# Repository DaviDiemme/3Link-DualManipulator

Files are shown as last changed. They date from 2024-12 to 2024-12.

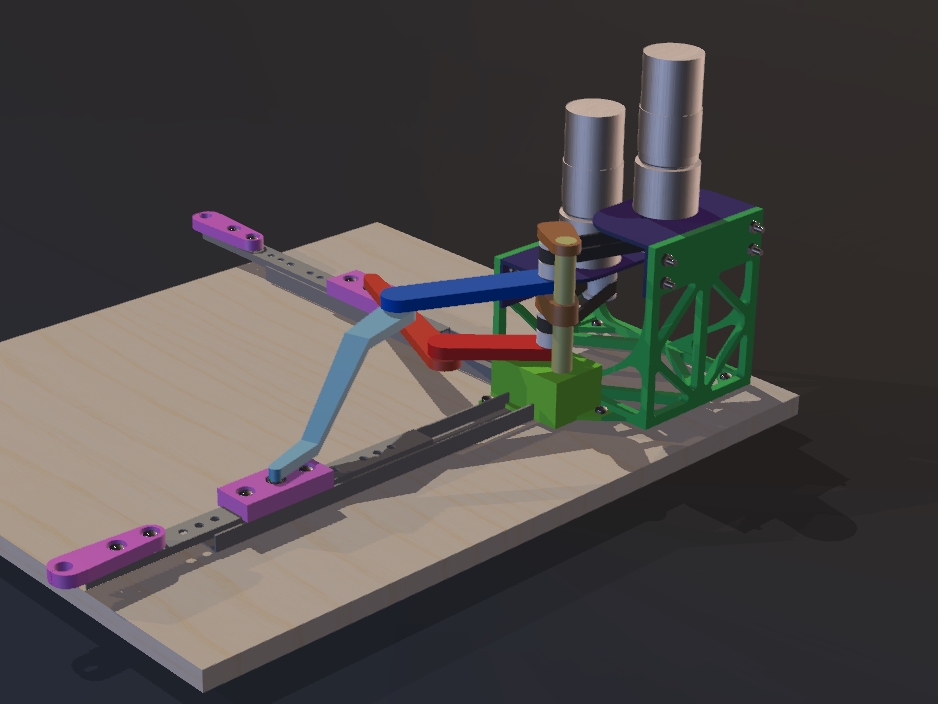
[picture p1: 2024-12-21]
images/robot render1 8.jpg

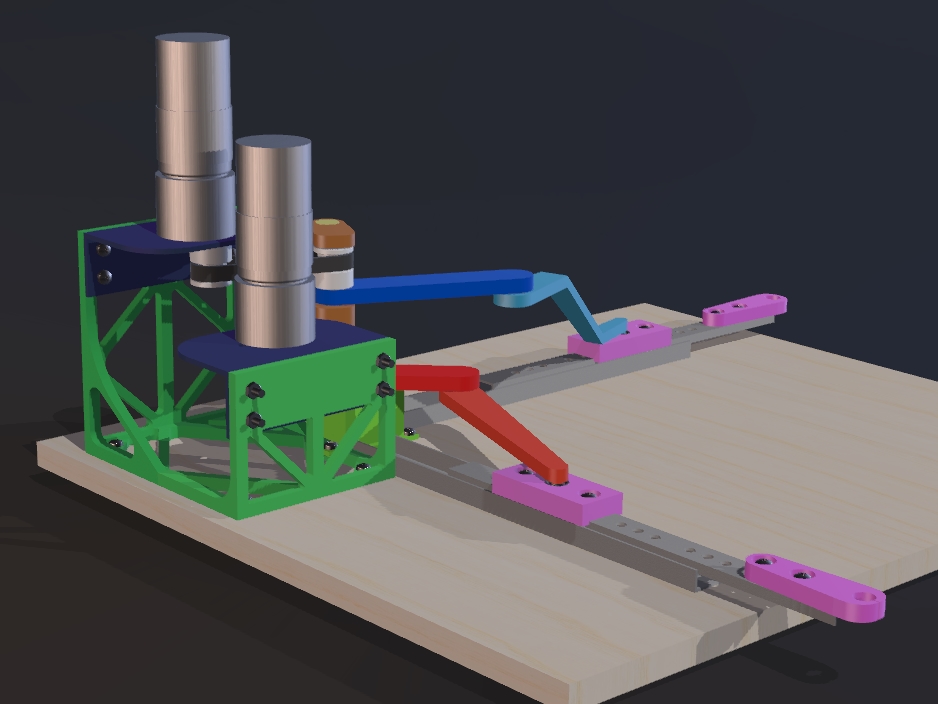
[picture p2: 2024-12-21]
images/robot render1 5.jpg

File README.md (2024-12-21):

robot render1 7

The device consists of a dual three-link manipulator with 2 actuators and 2 end-effectors on 
perpendicular axes.
The design process starts with the study of the 2D model of the robot and the evaluation of 
its kinematics. The workspace of the robot is then explored and, after considering several 
concepts, the most suitable design is assessed and explained.

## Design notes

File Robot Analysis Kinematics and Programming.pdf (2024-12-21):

Davide De Marco – DaviDiemme - GitHub - 122024

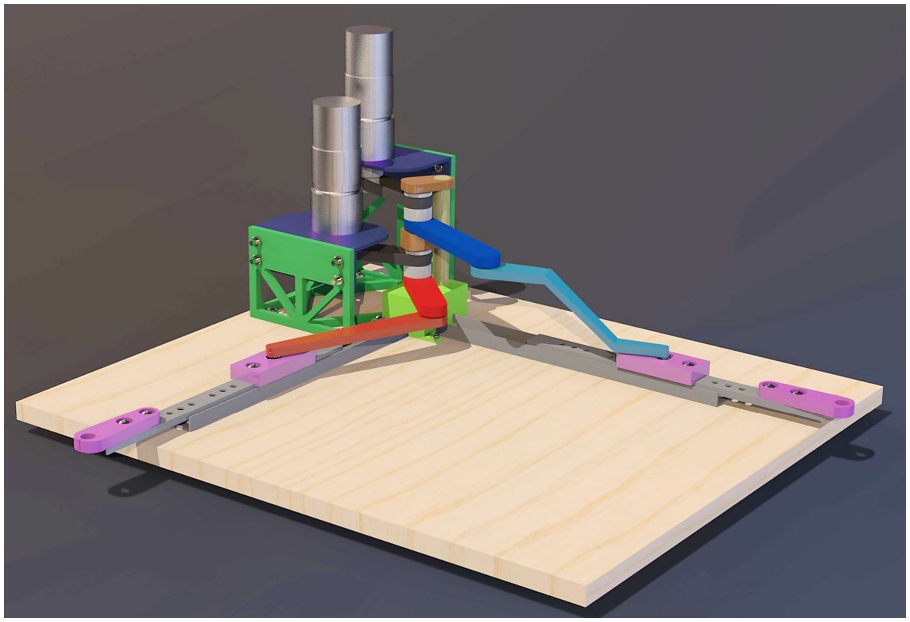
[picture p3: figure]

0

Introduction

The device consists of a dual three-link manipulator with 2 actuators and 2 end-effectors on perpendicular axes.

The design process starts with the study of the 2D model of the robot and the evaluation of its kinematics. The workspace of the robot is then explored and, after considering several concepts, the most suitable design is assessed and explained.

The programming is executed using MATLAB Simulink, also for the construction of the kinematics block diagrams.

First a closed-loop system is run to test the application of PID controller for running the DC motor, then the robot kinematics functions are built and implemented in the control system.

Tools and Components

The motors used are 2 simple EMG30 12 volts brushed motors, equipped with encoders and a gearbox reduction of 30:1, the encoders are used for the feedback signal in the control system.

The motors are driven by a RKL298 PCB, it can power up to two motors with the use of an external DC power supply and consists of an H-bridge drive chip that adjusts the rotation of each motor by controlling the polarity of the voltage applied to it, the sense of rotation depends on the combination of two inputs pins that come from the microcontroller. The speed of the motor is also regulated by the microcontroller sending Pulse Width Modulation -PWM- pulses to the motor driver.

1

The microcontroller stated is the Launchpad F28069M board by Texas Instruments interfaced with MATLAB, the code is generated by Code Composer Studio on the basis of a block diagram model built on Simulink.

Robot Kinematics
Due to the structure of the robot, the kinematics of the two manipulators is the same but on different axis and angles. Note that the shape of the robot leads to establish some limits to the movement of the actuators.
Each manipulator consists of 3 links and 3 joints, the first joint is attached to the actuator on the base, while the last one is fixed on a linear slider. The third link with the end-effector move along a defined axis and therefore the rotational movement of the actuator is converted into linear displacement. The two manipulators have a similar shape but with links of different lengths, that affect their workspace and movement.
Set 1)

The first manipulator lies on the horizontal axis.
The actuator is placed
on the base, and it is
considered as the origin
of the x-axis on which
the end-effector moves.

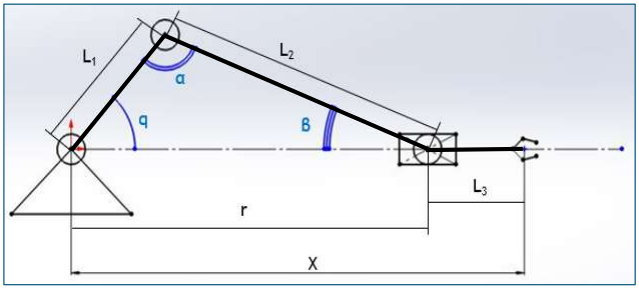
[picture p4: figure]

Forward Kinematics
Forward kinematics consists in the derivation of the total displacement X for any given angle of q. The lengths of the links are predefined while the angles change, of which only one is known.
The total displacement X is considered as the sum of L3 and the hypotenuse r of the triangle.

### 1. X = r + L

Two sides and one angle of the triangle are known; hence the third side r can be found using a few trigonometric functions:
From sine rule:
2.
=

=

To find r, angle α is needed, and it is derived from the subtraction of the triangle’s angles to the total of 180°.
First, angle β is calculated from sine

### 3. sin β =

and

Schematics for kinematics of first manipulator

2

### 4. β = sin(

sinq)

Now the third angle is derived

### 5. α = 180 − q − β

And r can be calculated as

### 6.1. r =

or 6.2. r =

Thus, the resultant displacement is equation 1. with the r found in either 6.1 or 6.2. Inverse Kinematics
Inverse kinematics is the derivation of the angle of the actuator q needed to achieve a desired displacement in X.
As for forward kinematics, the total displacement X is the sum of L3 and r, so for the solution of q, r is derived from X

### 7. r = X − L

Cosine rule can be applied to the triangle as in equation 8.

### 8. L

= r
+ L
| − 2rL cos q

From this equation, the angle q can be simply derived:

### 9. cosq =

and

### 10. q = cos(

)

For inverse kinematics, when coming to the resolution of the final angle, always the smallest value is taken, e.g. if cos¹
2

= 60° or 300° only 60 is considered. The angle of the first actuator is limited from 0 to 90°.

3

Set 2)

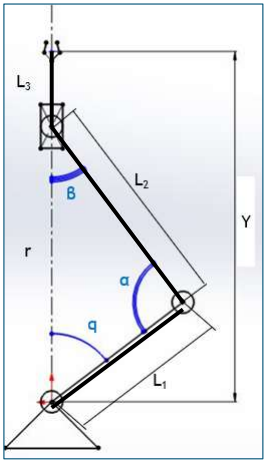
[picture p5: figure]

The second manipulator lies on the vertical axis. The actuator is placed on the base, aligned with the one of set 1, and it is considered as the origin of the y-axis on which the end-effector moves.
Forward Kinematics
Forward kinematics is the computation of the total displacement Y for a given angle q.
The total displacement Y is defined as

### 11. Y = r + L

Equations from 2 to 6 apply in the same way, but with the respective lengths and angle q, and the resulting r is used in equation 11.
Inverse Kinematics
Inverse kinematics is the derivation of the angle of the actuator q needed to achieve the desired vertical displacement in Y.

### 12. r = Y − L

Equations 8 to 10 are used in the same way, but with the respective lengths applied, and the resulting angle is always the smallest between y-axis and the first link L1.
Note that the value of second actuator is considered as negative and is limited from 0 to 60°. Workspace Analysis
The workspace derived from the robot kinematics is quite simple: the two end-effectors move along two perpendicular axes x and y. The robot moves on a 2D plane and has a total of 2 degrees of freedom.
Since, for building reason, limits are set to the actuators’ angle, the workspace only depends on the lengths of the links.
The workspace on the 2 axes goes from the minimum extension of

### 13. X = L

− L

+ L for q = 90°

### 14. Y =

L2 sinα
sinq + L for q = 60°

To the maximum of

### 15. L + L + L for q = q = 0°

For the prototype design the following lengths are used, in millimetres (mm):
SET | LINK 1 | LINK 2 | LINK 3
1 | 50 | 100 | 135
2 | 75 | 100 | 105

Schematics for kinematics of second manipulator

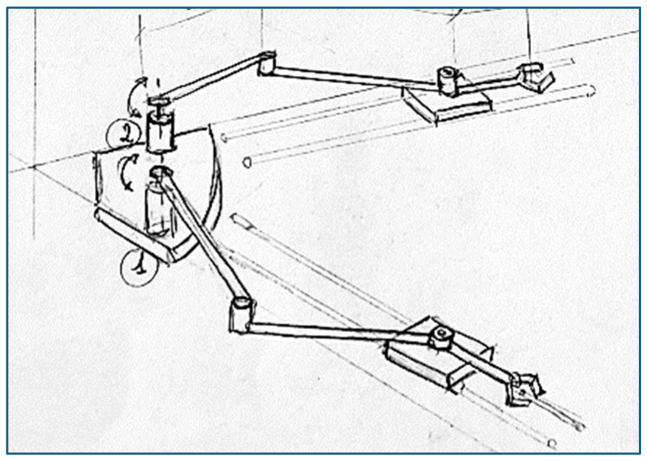
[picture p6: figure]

4

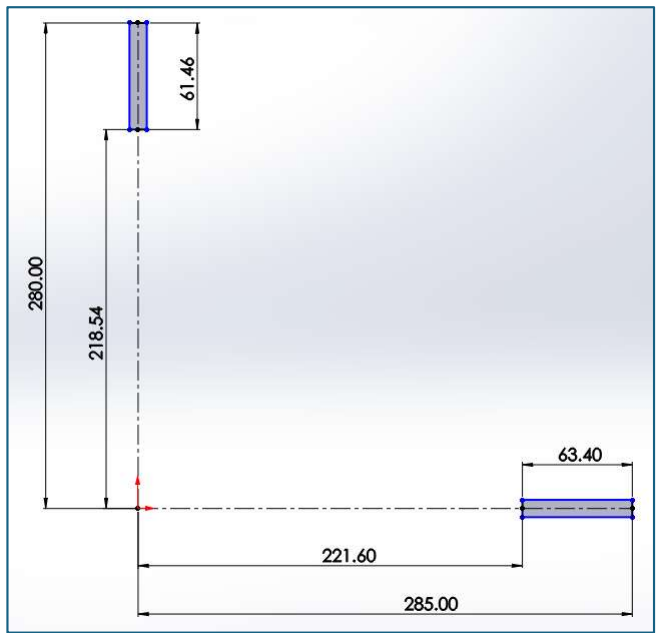
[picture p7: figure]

The workspace measured seems small and very limited, for the two manipulators it appears to be just above 60 mm.
This happens due to the concept and the application of the robot, the actuators cannot rotate fully otherwise there would be conflicts between the different parts that would interfere with each other, preventing the free movement of the manipulators.

General Design and Concept
The robot lies on a 2D plane and has 2 degrees of freedom which correspond to the linear movement of the end-effectors on the two axes of the plane. The first joints of the two manipulators are those connected to the actuators, they are placed on the base, and they are aligned to the same vertical z-axis, going out of the workspace plane.
The end joints and the two end-effectors are fixed on
linear slides; hence the third link is made up of a
carriage, the slide and the end effector. The rotational
movement of the joints is allowed by the use of small ball bearings.
For each actuator, the transmission of angular motion can be ensured by either different gear systems or with pulleys and belt between the motor and the first joint. For the purpose of this robot, the belt and pulley system is chosen as easy to make and accurate. Small and precise gear systems are difficult to print unless a high precision printer is used. Therefore, the two motors can be positioned away from the base but at a defined height that ensures the correct coupling of the belt on the pulleys.
For this concept, the two motors are fixed on the respective mounting brackets that are installed on vertical supports that holds the motors in position, at the correct height, and upside-down.

Workspace drawing with measures

Robot general concept sketch

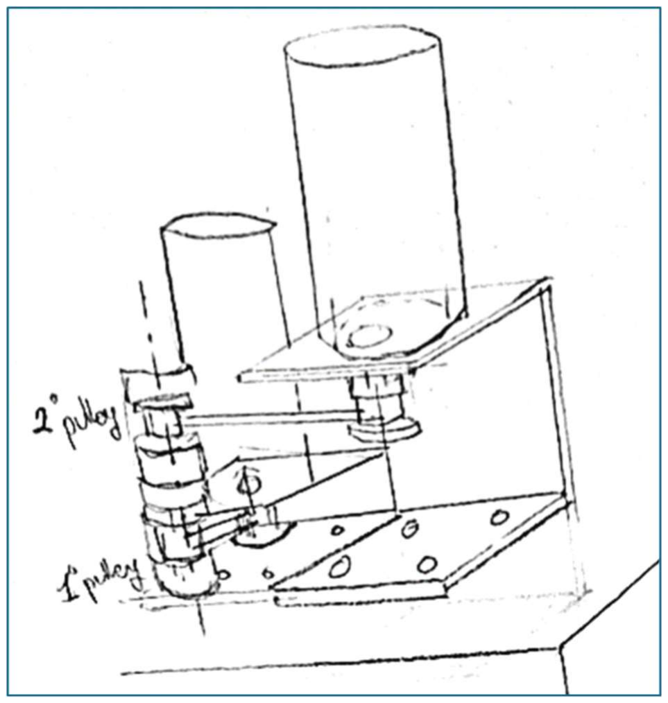
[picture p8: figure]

5

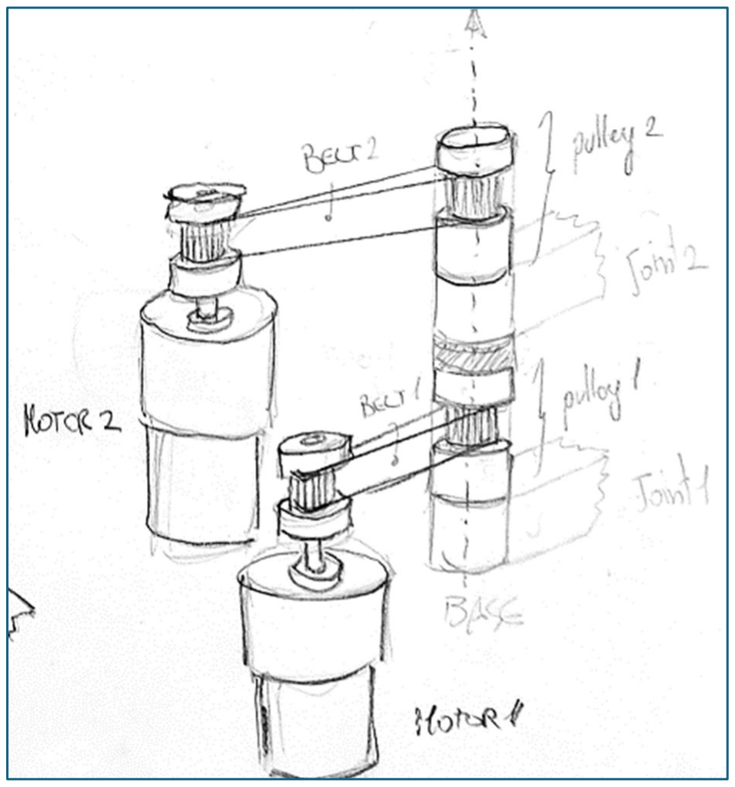
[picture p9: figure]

MATLAB Control Simulation
The program consists of a Simulink model which includes a closed-loop system with PID controller. The controller that takes the angular position of the motor from the encoders, compares it with a given input value and finally delivers a suitable voltage to achieve the exact position. The values of both the reference and the angular position are read in degrees, while the output signal from PID controller is in volts.
The control system design starts with the control test of one DC motor driven by a PID controller implemented within the program. The robot kinematics is then introduced, the respective block diagrams are assembled on Simulink, and subsequently implemented within the motor control diagram.

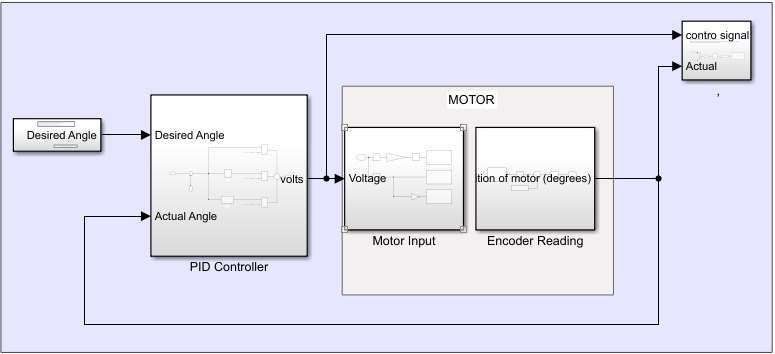
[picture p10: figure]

Control Diagram for one DC motor with PID controller
The PID - Proportional Integral Derivative - control consists in the regulation of a system’s behaviour based on the difference - error - between input signal and the real output signal achieved by the system. The controller is made up of three terms: the error, taken as function of time e(t), its integral and its derivative forms. The three components are first adjusted by some gain values, respectively Kp, Ki and Kd, and then added together to produce the appropriate control signal.

sketch of the pulley and belt system for motion transmission

sketch of the supports for the motors

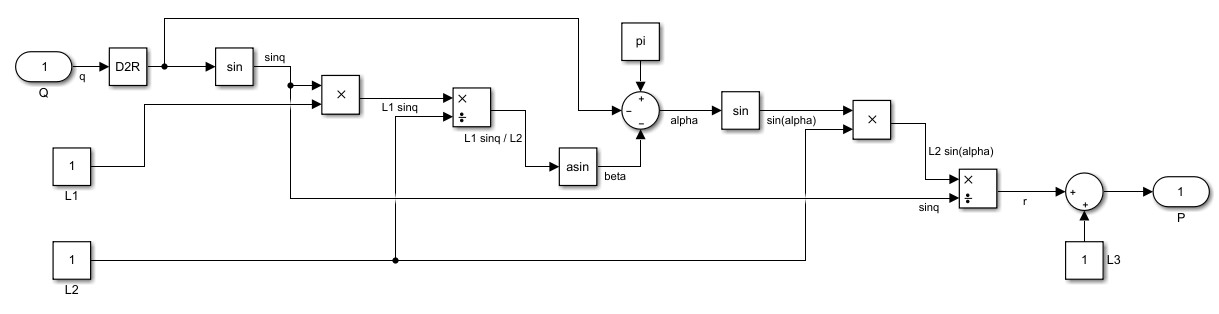
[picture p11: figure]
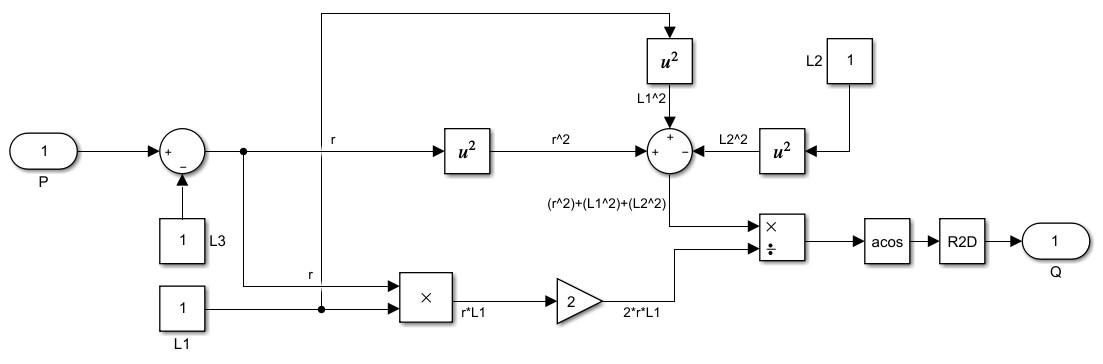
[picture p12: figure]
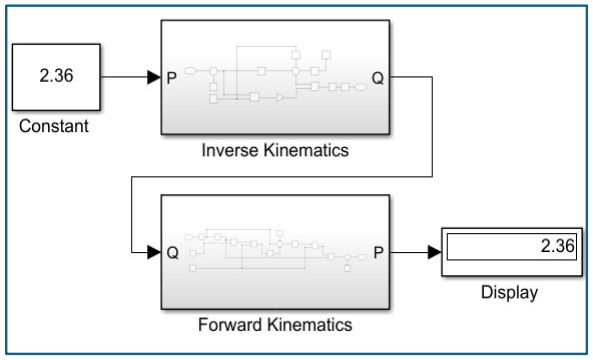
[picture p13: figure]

6

Once the program is uploaded on the board, the ‘desired angle’ and ‘actual angle’ signals are data exchanged between the microcontroller and the software through a serial communication port. By studying this system, the PID controller is tuned, and the gain values are set as the most suitable for the majority of motor angles and applications.
Robot kinematics is built and tested on Simulink. The block diagrams represent the mathematical equations for the forward and inverse kinematics.

Simulink block diagram for forward kinematics

Simulink block diagram for inverse kinematics
It is important to consider that for the kinematics calculations on Simulink input angles must be converted from degree to radians, vice versa for output angles. P stays for position of end-effector while Q is the angular displacement of the actuator.
The two block diagrams are referred to as subsystems, and they are inserted in the same Simulink model and connected together to verify that the outcome of the calculations is always correct for both subsystems.

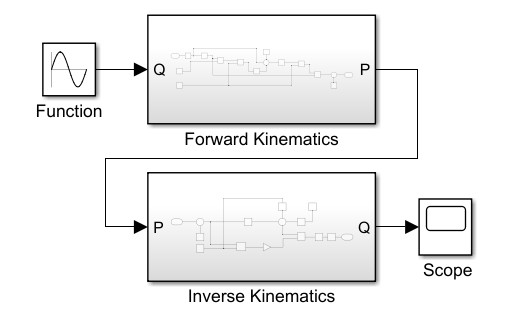
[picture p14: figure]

kinematics results check 1 | kinematics results check 2

7

Once the kinematic blocks have proven to work correctly, the algorithms are implemented in the Simulink control diagram with the PID controller for the DC motor.

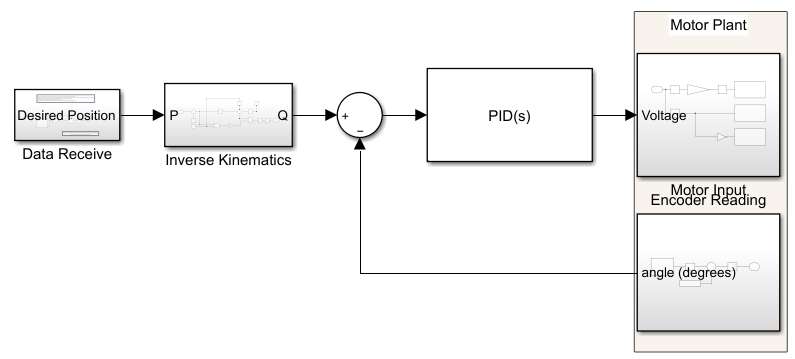
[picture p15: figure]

Simulink block diagram of kinematics PID controller for the robot
The two kinematics blocks can be interchanged according to the application of the device, or they can be used together, changing the type of error signal:

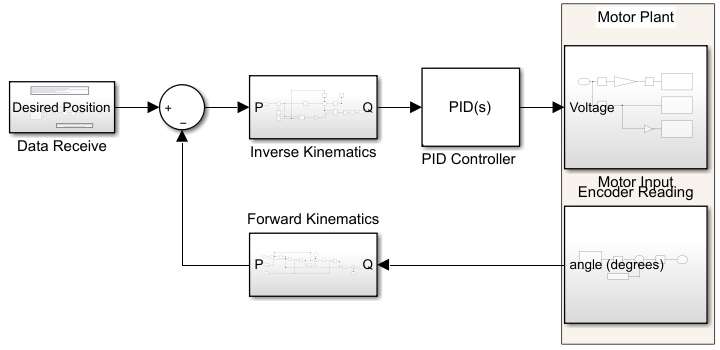
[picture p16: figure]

Simulink block diagram of kinematics PID controller for the robot 2

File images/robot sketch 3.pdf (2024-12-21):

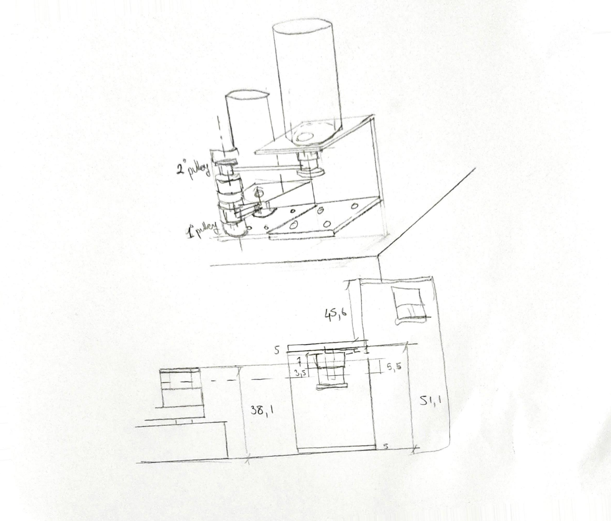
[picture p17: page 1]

6 | o

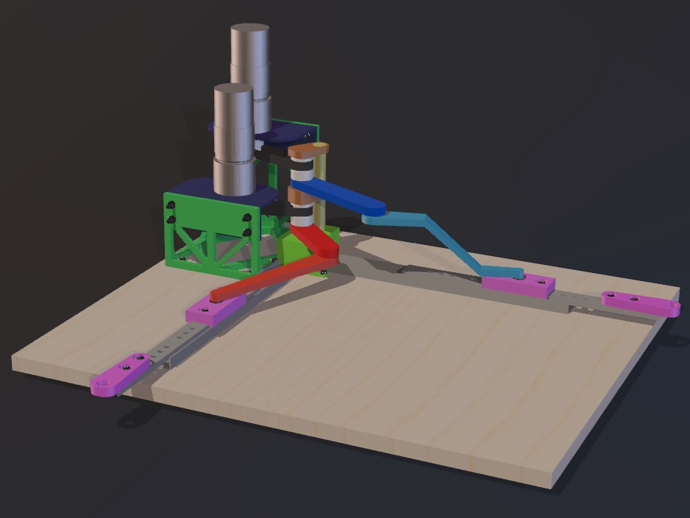
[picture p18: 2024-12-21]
images/robot render1 7.jpg

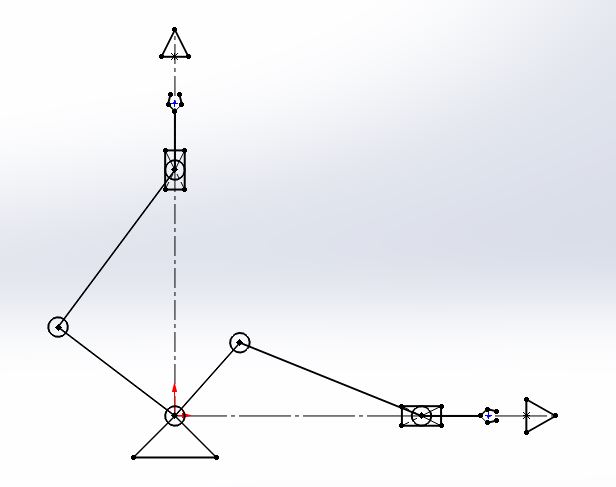
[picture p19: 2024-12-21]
images/2D first sketch.JPG

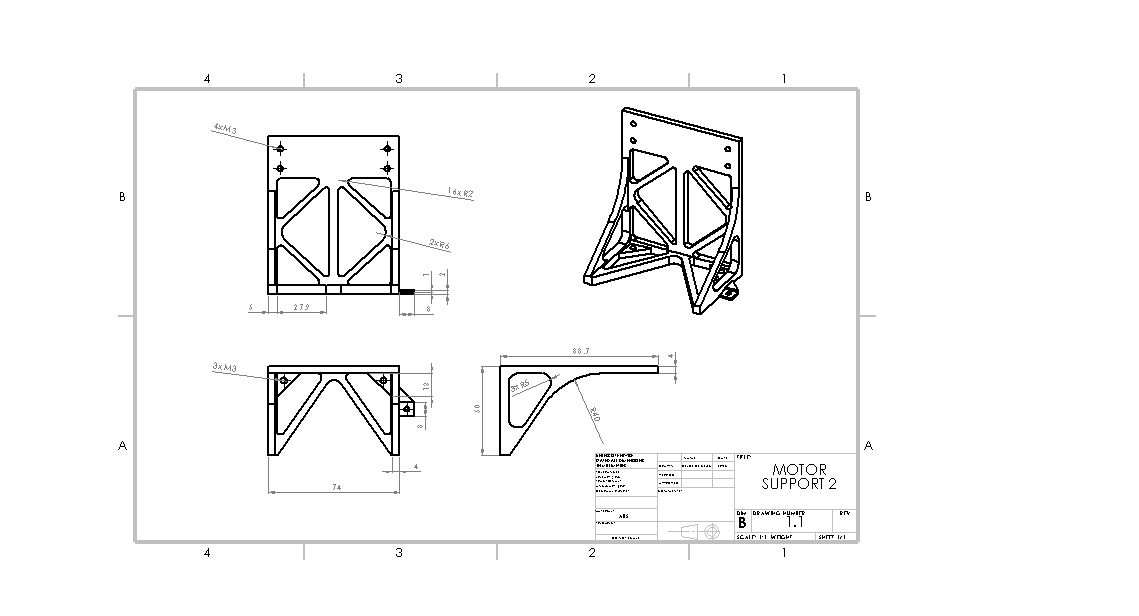
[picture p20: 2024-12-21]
technical drawings/base motor2 drawing.JPG

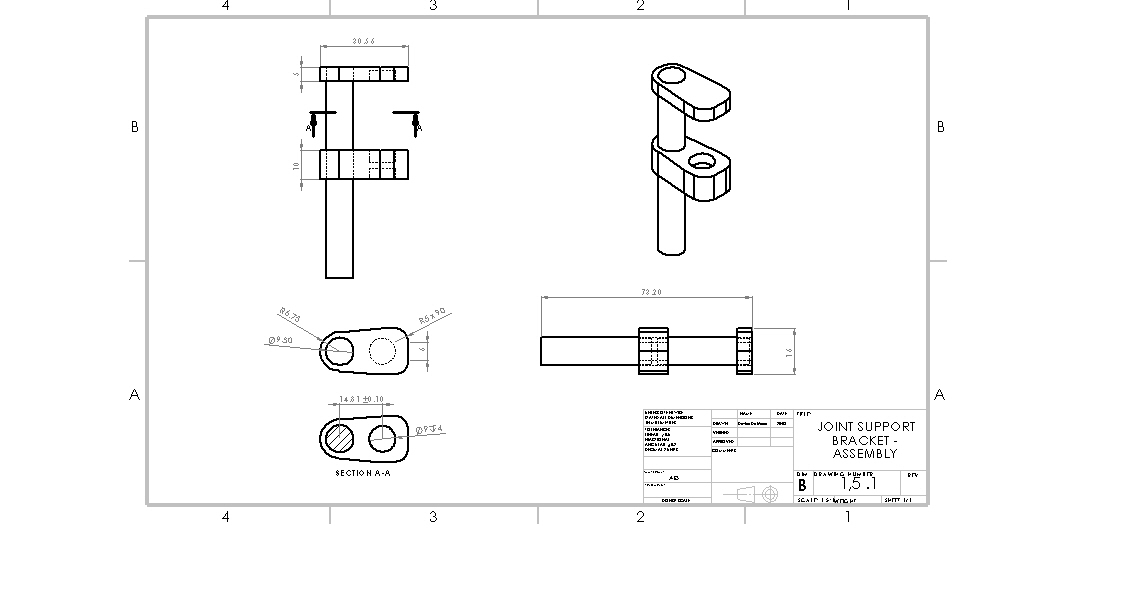
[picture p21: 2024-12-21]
technical drawings/joint support bracket drawing.JPG

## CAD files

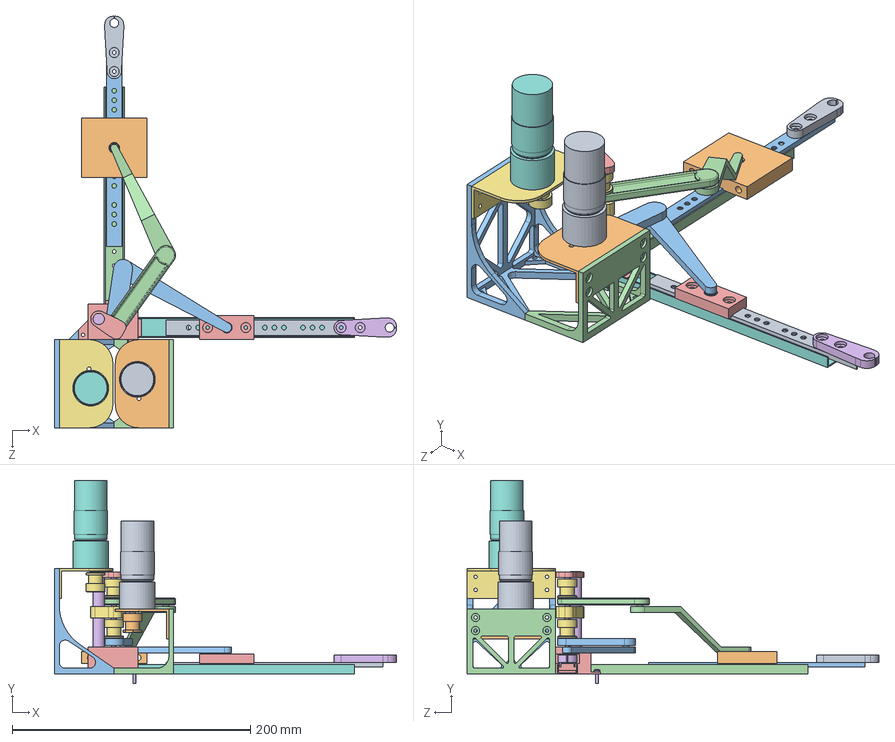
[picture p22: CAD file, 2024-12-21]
SolidWorks parts/Assem1.SLDASM
287.1 x 170.8 x 345.6 mm
base motor2
base motor1
base joint
motor mounting bracket x 2
motor x 2
motor shaft x 2
pulley x 4
base link1
base link2
perno x 2
wooden rod
rod2joints
rod2joints top
slide1 x 2
slide2 x 2
ISO 1224 - 380409 - R,10,SI,NC,10_68 x 8
end link
end link2
carrello x 2
end effector x 2

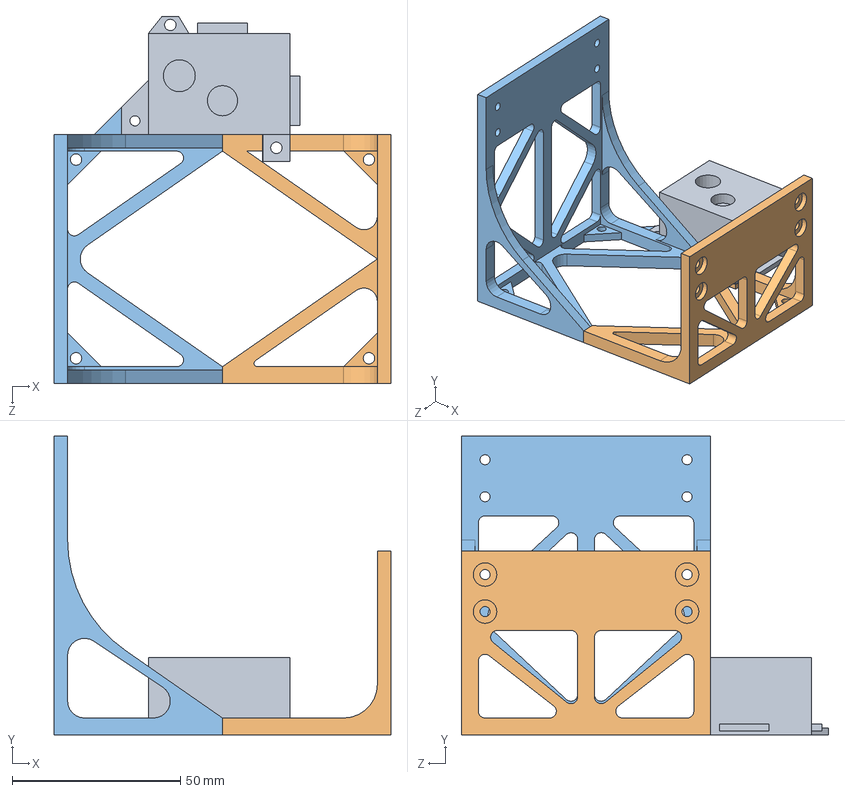
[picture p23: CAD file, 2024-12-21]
SolidWorks parts/Assem2.SLDASM
100.0 x 88.7 x 109.0 mm
base joint
base motor1
base motor2

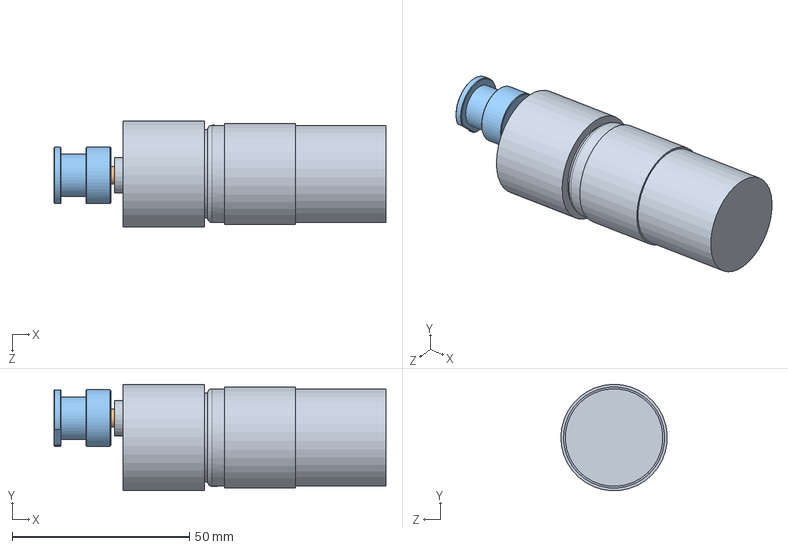
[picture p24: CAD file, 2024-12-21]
SolidWorks parts/motor-pulley.SLDASM
93.6 x 30.0 x 30.0 mm
motor
motor shaft
pulley

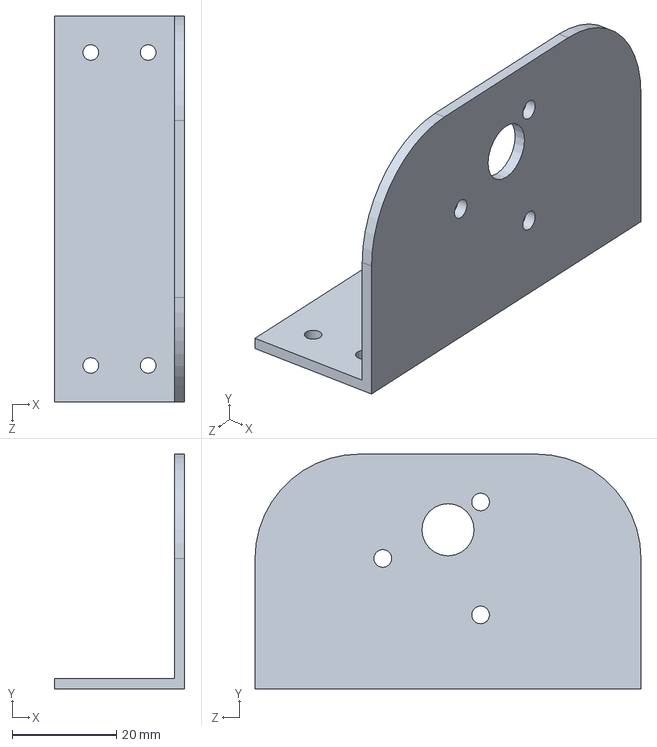
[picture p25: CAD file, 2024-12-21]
SolidWorks parts/motor mounting bracket.SLDPRT
25.0 x 45.0 x 74.0 mm

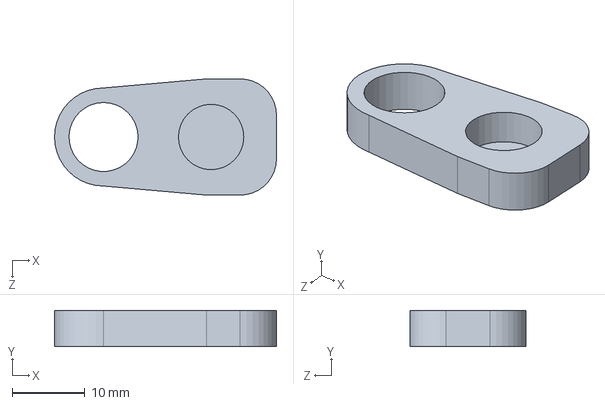
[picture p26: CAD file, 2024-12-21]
SolidWorks parts/rod2joints top.SLDPRT
30.6 x 5.00 x 16.0 mm

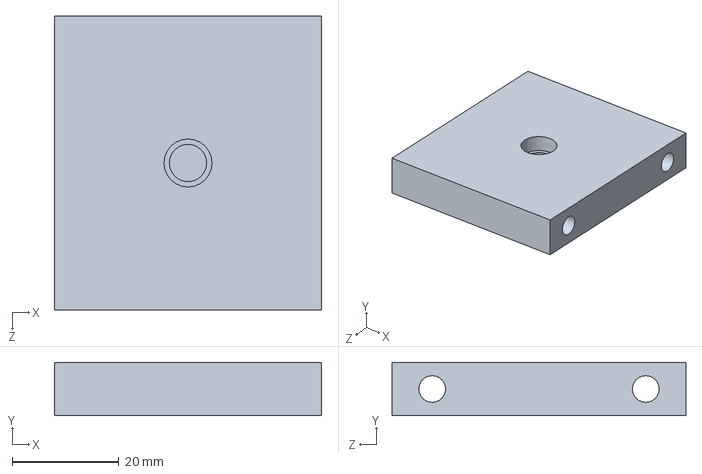
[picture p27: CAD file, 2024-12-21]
SolidWorks parts/carrello.SLDPRT
50.0 x 10.0 x 55.0 mm

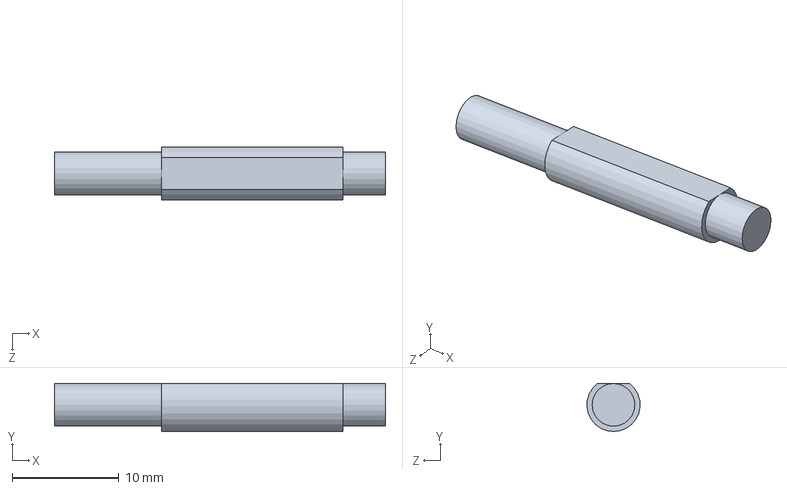
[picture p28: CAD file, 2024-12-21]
SolidWorks parts/perno.SLDPRT
31.0 x 4.50 x 4.99 mm

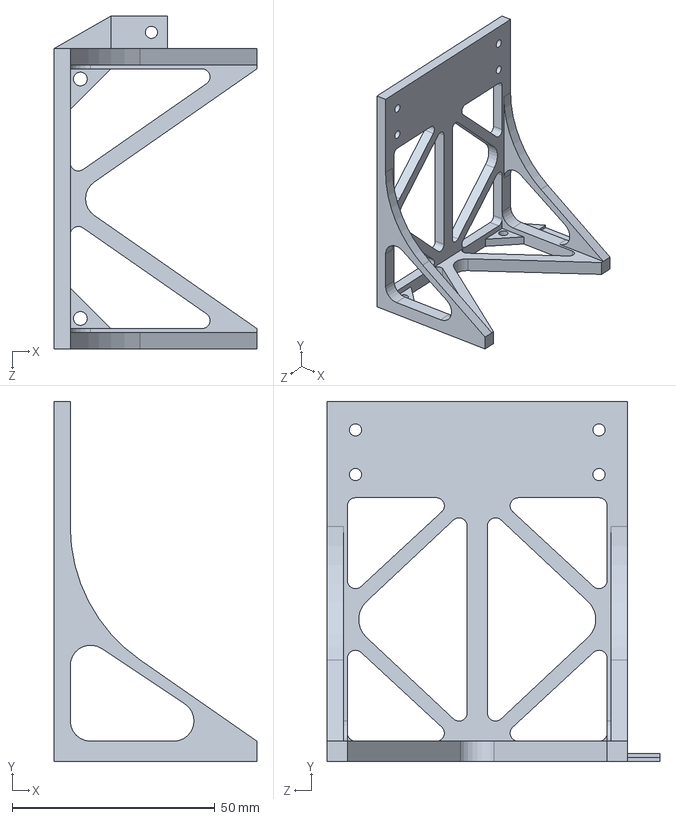
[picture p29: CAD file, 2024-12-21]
SolidWorks parts/base motor2.sldprt
50.0 x 88.7 x 82.0 mm

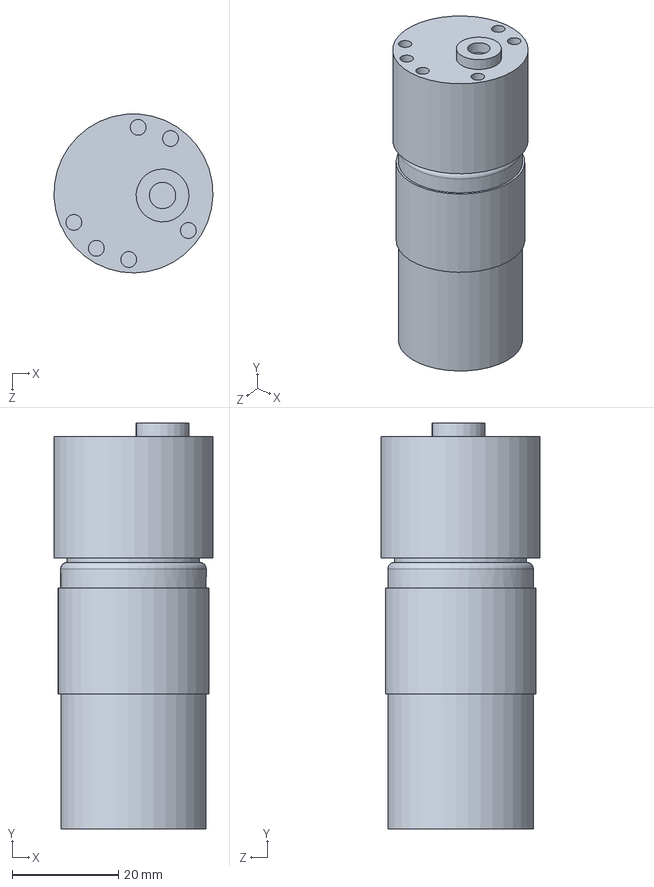
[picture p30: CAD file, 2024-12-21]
SolidWorks parts/motor.SLDPRT
30.0 x 76.6 x 30.0 mm

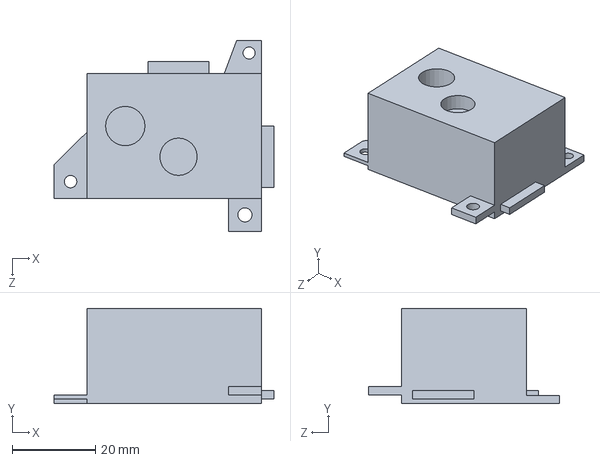
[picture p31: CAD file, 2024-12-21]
SolidWorks parts/base joint.sldprt
53.0 x 23.0 x 46.0 mm

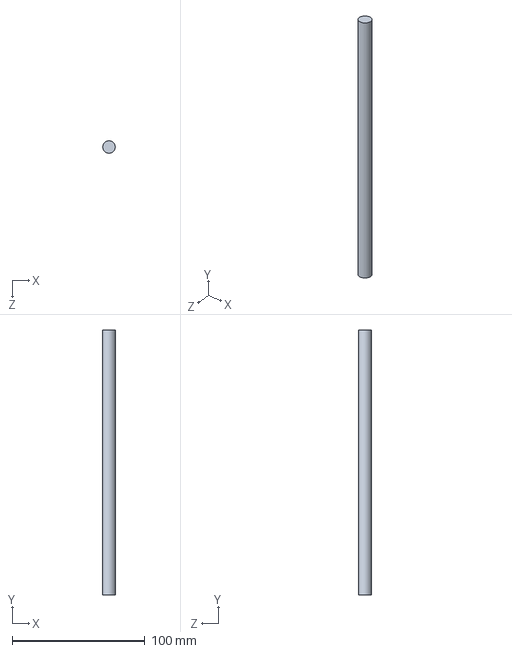
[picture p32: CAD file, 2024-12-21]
SolidWorks parts/wooden rod.SLDPRT
9.50 x 200.0 x 9.50 mm

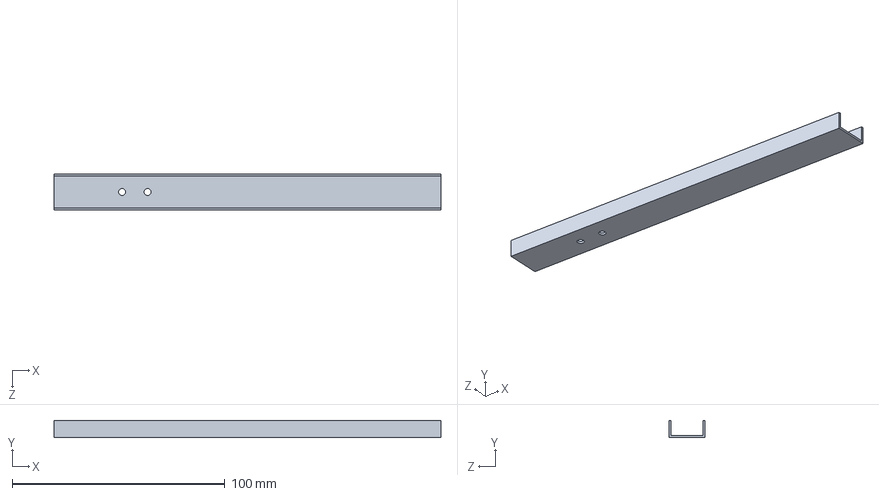
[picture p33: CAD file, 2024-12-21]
SolidWorks parts/slide1.SLDPRT
182.0 x 8.00 x 17.0 mm

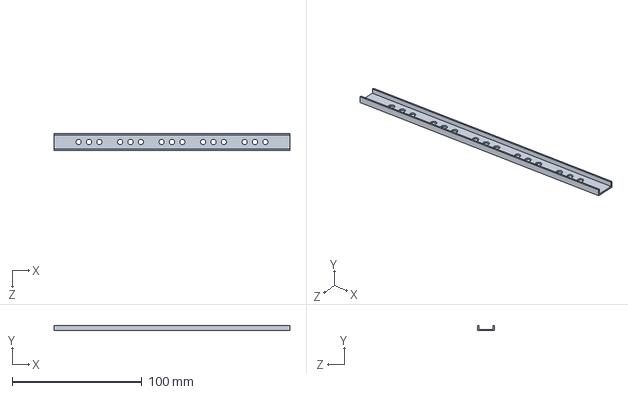
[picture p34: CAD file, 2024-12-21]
SolidWorks parts/slide2.sldprt
182.0 x 4.00 x 13.0 mm

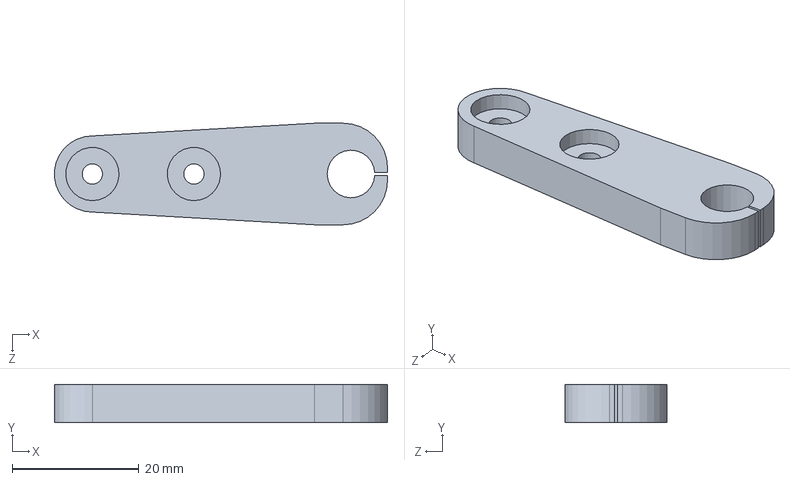
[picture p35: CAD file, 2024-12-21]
SolidWorks parts/end effector.SLDPRT
52.5 x 6.00 x 16.0 mm

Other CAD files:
SolidWorks parts/base assembly.SLDASM
SolidWorks parts/end link2.SLDPRT
SolidWorks parts/motor shaft.SLDPRT
SolidWorks parts/pulley.SLDPRT
SolidWorks parts/base assembly.SLDDRW
SolidWorks parts/base joint.SLDDRW
SolidWorks parts/base link1.SLDPRT
SolidWorks parts/base link2.SLDPRT
SolidWorks parts/base motor1.SLDDRW
SolidWorks parts/base motor1.sldprt
SolidWorks parts/base1.SLDPRT
SolidWorks parts/end link.SLDPRT
SolidWorks parts/robot_sketch1.SLDPRT
SolidWorks parts/rod2joints.SLDPRT
